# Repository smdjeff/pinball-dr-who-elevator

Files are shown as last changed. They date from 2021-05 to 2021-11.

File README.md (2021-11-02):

# dr-who

Replacement elevator mechanism for the Dr Who pinball machine. 

https://en.wikipedia.org/wiki/Doctor_Who_(pinball)

https://youtu.be/fHkql48IPpg

https://youtu.be/L-MsUkgBwkI

<table><tr>
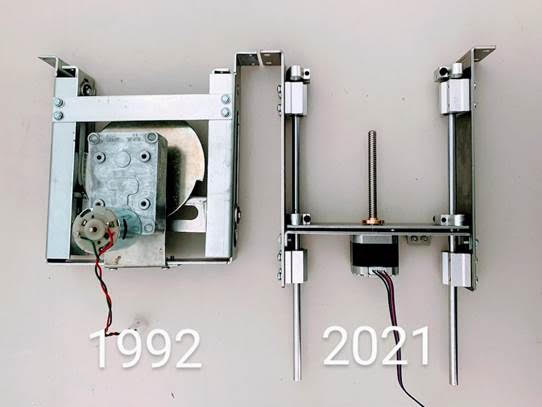
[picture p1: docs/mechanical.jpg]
<td rowspan="2"></td>
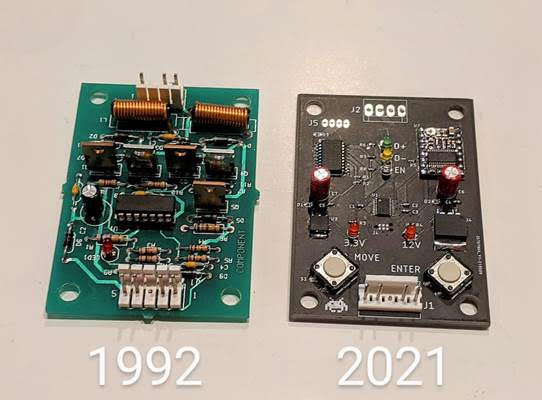
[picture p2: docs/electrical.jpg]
<td rowspan="2"></td>
</tr>
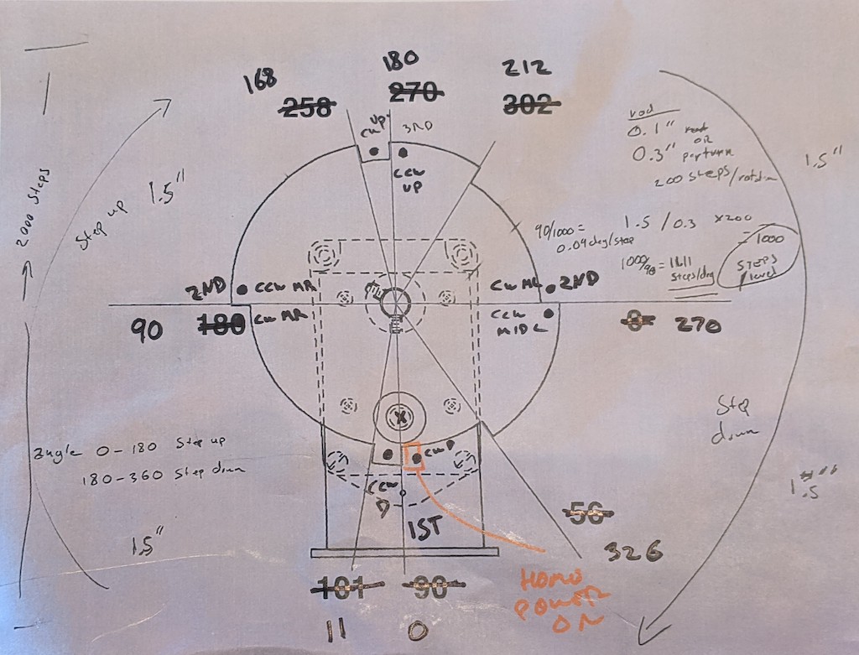
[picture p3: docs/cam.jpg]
<tr><td></td></tr>
</table>

## Firmware
* Drop in replacement to original system
* Uses simulated cam stimulus into factory system
* Passes factory diagnostics tests 

## Electronics
* Custom electronics
* Drop in replacement for bi-directional motor board A-15782
* Modern current limiting for saftey
* Modern acceleration and deceleration profiles for smooth start and stop

## Mechanical
* Custom brackets - laser cut and bent
* Standard desktop CNC stepper motor, rod, and nut.
* Replaces original parts
  * Cam A-15035
  * Motor 14-7970
  * Bracket A-15037
  * Support Bracket A-15036
  * Roller 02-4764

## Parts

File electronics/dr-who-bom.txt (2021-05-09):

Partlist exported from /Users/jmathews/Documents/EAGLE/projects/dr-who.sch at 5/8/21 1:46 PM

Part Value         Device                           Package                 Description                                                               MF    MPN           OC_FARNELL OC_NEWARK POPULARITY PROD_ID   VALUE
C1   4.7uF         4.7UF0603                        0603                    4.7µF ceramic capacitors                                                                                                      CAP-08280 4.7uF
C2   0.1uF         0.1UF-0603-25V-(+80/-20%)        0603                    0.1µF ceramic capacitors                                                                                                      CAP-00810 0.1uF
C3   0.1uF         0.1UF-0603-25V-(+80/-20%)        0603                    0.1µF ceramic capacitors                                                                                                      CAP-00810 0.1uF
C4   0.47uF        470PF-0603-50V-5%                0603                    470pF ceramic capacitors                                                                                                      CAP-07884 470pF
C5   0.47uF        470PF-0603-50V-5%                0603                    470pF ceramic capacitors                                                                                                      CAP-07884 470pF
C6   100uF         100UF-POLAR-RADIAL-2.5MM-25V-20% CPOL-RADIAL-2.5MM-6.5MM 100µF polarized capacitors                                                                                                    CAP-08439 100uF
C7   100uF         100UF-POLAR-RADIAL-2.5MM-25V-20% CPOL-RADIAL-2.5MM-6.5MM 100µF polarized capacitors                                                                                                    CAP-08439 100uF
D1                 DIODE-SOD323-R                   SOD323-R                DIODE                                                                                                              4                         
D2                 DIODE-SOD323-R                   SOD323-R                DIODE                                                                                                              4                         
D3                 DIODE-SOD323-R                   SOD323-R                DIODE                                                                                                              4                         
J1                 KK-156-5                         KK-156-5                KK 156 HEADER                                                             MOLEX               unknown    unknown   0                         
J2                 KK-156-4                         KK-156-4                KK 156 HEADER                                                             MOLEX               unknown    unknown   0                         
J4                 TC2030-MCP-NL                    TC2030-MCP-NL           TAG-CONNECT ICSP ConnectorManufacturer: Tag-Connect                                                                                          
J5                 PINHD-1X4                        1X04                    PIN HEADER                                                                                                         91                        
LED1 3.3V          LED3MM                           LED3MM                  LED                                                                                                                97                        
LED2 12V           LED3MM                           LED3MM                  LED                                                                                                                97                        
LED3 D+            LED3MM                           LED3MM                  LED                                                                                                                97                        
LED4 D-            LED3MM                           LED3MM                  LED                                                                                                                97                        
LED5 EN            LED3MM                           LED3MM                  LED                                                                                                                97                        
R1   10k           10KOHM-0603-1/10W-1%             0603                    10kΩ resistor                                                                                                                 RES-00824 10k  
R2   10k           10KOHM-0603-1/10W-1%             0603                    10kΩ resistor                                                                                                                 RES-00824 10k  
R3   650           10KOHM-0603-1/10W-1%             0603                    10kΩ resistor                                                                                                                 RES-00824 10k  
R4   5k            10KOHM-0603-1/10W-1%             0603                    10kΩ resistor                                                                                                                 RES-00824 10k  
R5   100k          10KOHM-0603-1/10W-1%             0603                    10kΩ resistor                                                                                                                 RES-00824 10k  
R6   470           10KOHM-0603-1/10W-1%             0603                    10kΩ resistor                                                                                                                 RES-00824 10k  
R7   470           10KOHM-0603-1/10W-1%             0603                    10kΩ resistor                                                                                                                 RES-00824 10k  
R8   470           10KOHM-0603-1/10W-1%             0603                    10kΩ resistor                                                                                                                 RES-00824 10k  
S1   MOVE          40/XX                            B3F/40XX                OMRON SWITCH                                                                                  unknown    unknown   0                         
S2   ENTER         40/XX                            B3F/40XX                OMRON SWITCH                                                                                  unknown    unknown   0                         
U1   STM32L011F3P6 STM32L011F3P6                    TSSOP20-I               IC                                                                                                                                           
U2   2977-DRV8825  2977-DRV8825                     DRV8825                 DRV8825 Stepper Motor Driver Carrier; High Current (Bulk; No Header Pins)                                                                    
U3   LM2936DT-3.3  LM2936DT-3.3                     TO252                   Ultra-Low Quiescent Current LDO Voltage Regulator                               BD433M5FP-CE2 1286863    26M0361   0                         
U4   LM2936D2PAK   LM2936D2PAK                      D2PAK                   Ultra-Low Quiescent Current LDO Voltage Regulator                                                                                            
U5   MAX333ACWP    MAX333ACWP                       SO20L                   ANALOG SWITCH                                                             MAXIM MAX333ACWP+   9725547    28K3302   0

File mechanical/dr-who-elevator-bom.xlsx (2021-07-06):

Table 1
Price sub | QTY | Part number
$8.23 | 1 | 500001 | Travel plate
$14.50 | 2 | 500002 | Side plate
$12.84 | 1 | 500003 | Motor plate
$0.00 | 0 | 500004-1 | Support shaft | Not used
$9.99 | 2 | 500004-2 | Support shaft
$11.98 | 4 | PN? | Bearing slide | 8mm
$9.99 | 2 | PN? | Rod | 8mm x 300mm
$25.99 | 1 |  | Stepper w/ rod | T8 100mm | What’s the spec on this? Comes with cable?
$0.00 | 1 | PN? | Rod nut
$0.58 | 1 | PN? | Micro switch
$3.00 | 1 |  | Screws | Specs?
$25.00 | 1 |  | PCB ASSY
$122.10

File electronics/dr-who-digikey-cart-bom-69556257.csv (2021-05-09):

# | QUANTITY | PART NUMBER | MANUFACTURER PART NUMBER | DESCRIPTION | CUSTOMER REFERENCE | BACKORDER | UNIT PRICE | EXTENDED PRICE
1 | 10 | 311-4047-1-ND | CC0603KRX5R9BB474 | CAP CER 0.47UF 50V X5R 0603 | C4,C5 | 0 | 0.35800 | 3.58
2 | 10 | 732-8825-1-ND | 860020473008 | CAP ALUM 100UF 20% 25V RADIAL | C6,C7 | 0 | 0.13000 | 1.30
3 | 15 | 1727-1228-1-ND | PMEG2010EA,135 | DIODE SCHOTTKY 20V 1A SOD323 | D1,D2,D3 | 0 | 0.28400 | 4.26
4 | 5 | A19903-ND | 640388-5 | CONN HEADER VERT 5POS 3.96MM | J1 | 0 | 0.37000 | 1.85
5 | 5 | A19902-ND | 640388-4 | CONN HEADER VERT 4POS 3.96MM | J2 | 0 | 0.32000 | 1.60
6 | 10 | 311-10KLECT-ND | AC0603JR-0710KL | RES SMD 10K OHM 5% 1/10W 0603 | R1,R2 | 0 | 0.02400 | 0.24
7 | 10 | SW411-ND | B3F-4000 | SWITCH TACTILE SPST-NO 0.05A 24V | S1,S2 | 0 | 0.44600 | 4.46
8 | 5 | BD433M5FP-CE2CT-ND | BD433M5FP-CE2 | IC REG LINEAR 3.3V 500MA TO252-3 | U3 | 0 | 1.07000 | 5.35
9 | 5 | LM2940CSX-12/NOPBCT-ND | LM2940CSX-12/NOPB | IC REG LIN 12V 1A DDPAK/TO263-3 | U4 | 0 | 1.93000 | 9.65
10 | 10 | 311-3567-1-ND | CC0603KPX7R9BB104 | CAP CER 0.1UF 50V X7R 0603 | C2,C3 | 0 | 0.06200 | 0.62
11 | 10 | 311-1455-1-ND | CC0603KRX5R6BB475 | CAP CER 4.7UF 10V X5R 0603 | C1 | 0 | 0.19500 | 1.95
12 | 10 | 311-10.0KHRCT-ND | RC0603FR-0710KL | RES SMD 10K OHM 1% 1/10W 0603 | R1,R2 | 0 | 0.02400 | 0.24
13 | 10 | 311-649HRCT-ND | RC0603FR-07649RL | RES SMD 649 OHM 1% 1/10W 0603 | R3 | 0 | 0.02400 | 0.24
14 | 10 | 311-2629-1-ND | RT0603DRE075K05L | RES SMD 5.05KOHM 0.5% 1/10W 0603 | R4 | 0 | 0.09200 | 0.92
15 | 10 | 311-100KHRCT-ND | RC0603FR-07100KL | RES SMD 100K OHM 1% 1/10W 0603 | R5 | 0 | 0.02400 | 0.24
16 | 10 | 478-7798-1-ND | SD0603S040S0R2 | DIODE SCHOTTKY 40V 200MA 0603 | D1,D2,D3 | 0 | 0.30200 | 3.02
17 | 10 | 311-470DCT-ND | RT0603DRD07470RL | RES SMD 470 OHM 0.5% 1/10W 0603 | R6,R7,R8 | 0 | 0.14400 | 1.44
18 | 10 | 732-5006-ND | 151031SS06000 | LED RED DIFFUSED 3MM ROUND T/H |  | 0 | 0.17000 | 1.70
19 | 10 | 732-5008-ND | 151031VS06000 | LED GREEN DIFFUSED 3MM ROUND T/H |  | 0 | 0.16000 | 1.60
20 | 10 | 732-5009-ND | 151031YS05900 | LED YELLOW DIFF 3MM ROUND T/H |  | 0 | 0.17000 | 1.70

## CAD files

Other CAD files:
mechanical/500002.dwg
mechanical/500003.dwg
mechanical/500001.dwg

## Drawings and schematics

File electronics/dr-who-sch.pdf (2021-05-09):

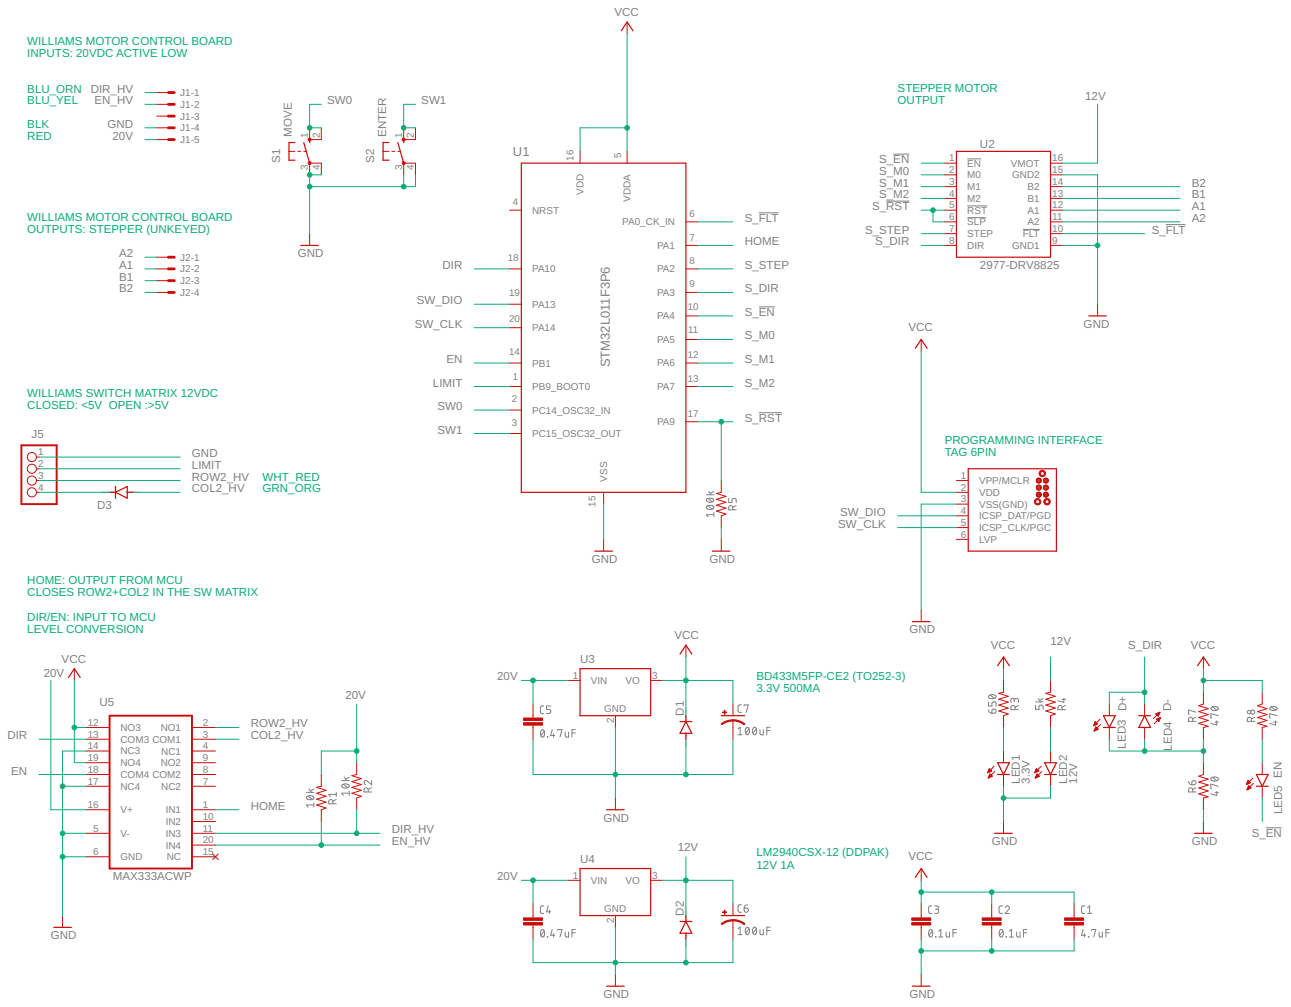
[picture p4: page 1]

WILLIAMS MOTOR CONTROL BOARD
INPUTS: 20VDC ACTIVE LOW

OUTPUTS: STEPPER (UNKEYED)

HOME: OUTPUT FROM MCU
CLOSES ROW2+COL2 IN THE SW MATRIX

DIR/EN: INPUT TO MCU
LEVEL CONVERSION

SpiceOrder 1 SpiceOrder 2

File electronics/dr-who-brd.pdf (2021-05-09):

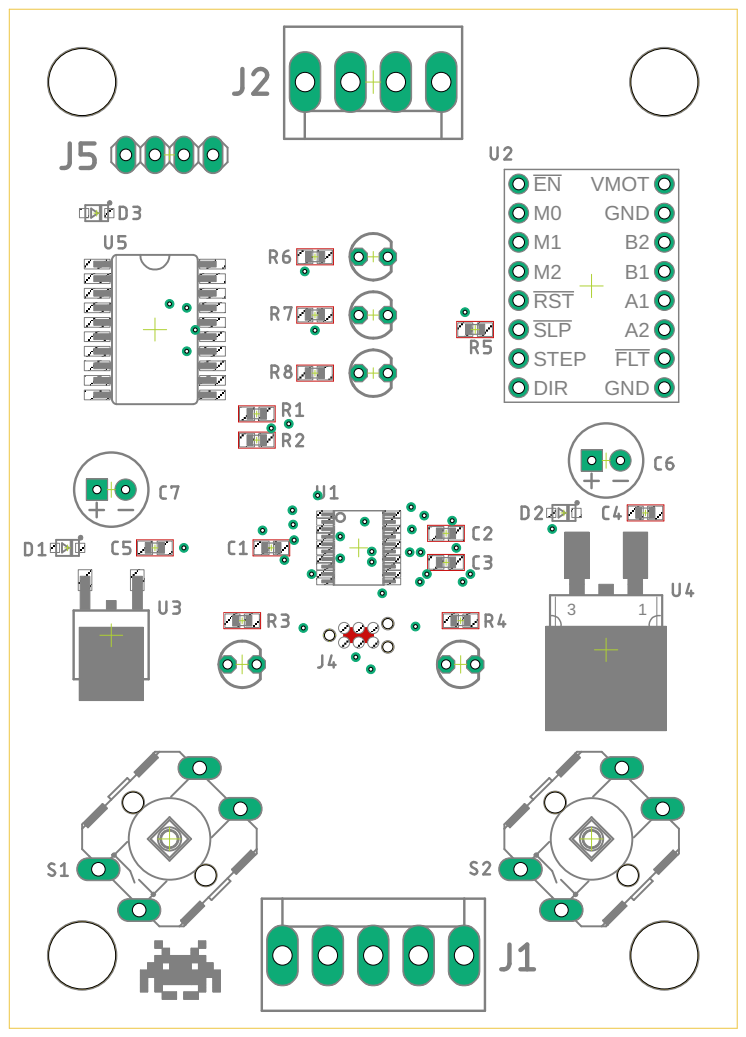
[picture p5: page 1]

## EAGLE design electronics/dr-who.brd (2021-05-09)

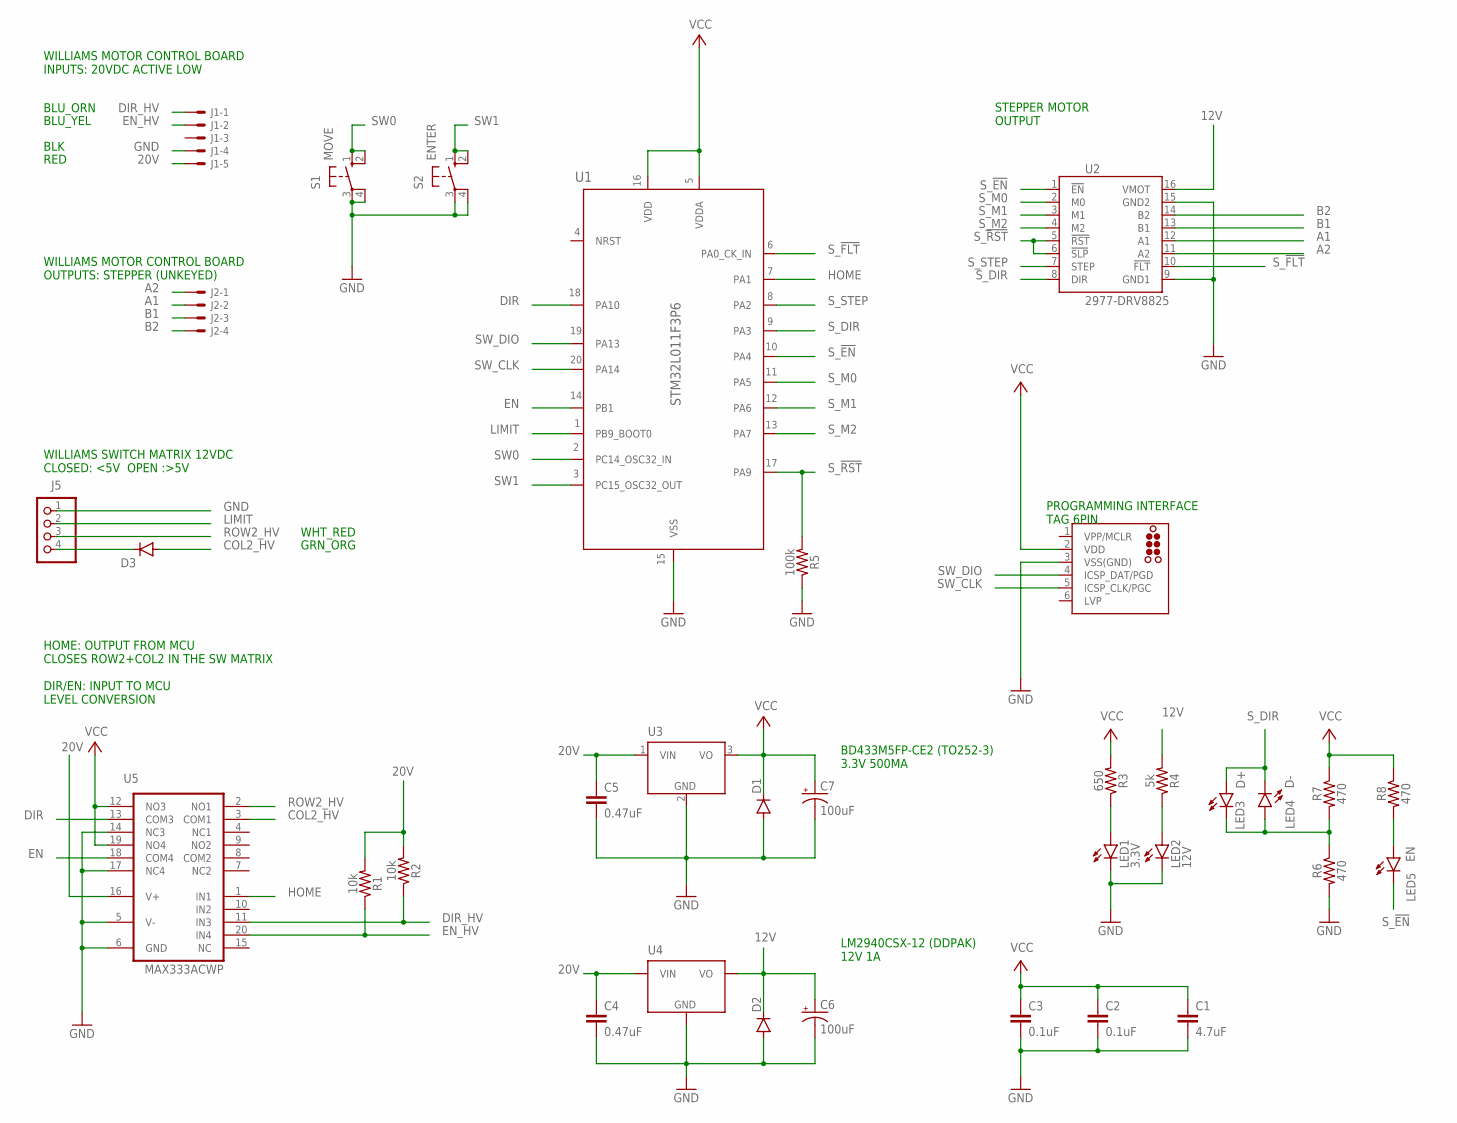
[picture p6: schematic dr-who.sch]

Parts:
C1: 4.7uF; 0603
C2, C3: 0.1uF; 0603
C4, C5: 0.47uF; 0603
C6, C7: 100uF; CPOL-RADIAL-2.5MM-6.5MM
D1, D2, D3: DIODE-SOD323-R; SOD323-R
J1: KK-156-5
J2: KK-156-4
J4: TC2030-MCP-NL
J5: PINHD-1X4; 1X04
LED1: 3.3V; LED3MM
LED2: 12V; LED3MM
LED3: D+; LED3MM
LED4: D-; LED3MM
LED5: EN; LED3MM
R1, R2: 10k; 0603
R3: 650; 0603
R4: 5k; 0603
R5: 100k; 0603
R6, R7, R8: 470; 0603
S1: MOVE; B3F/40XX
S2: ENTER; B3F/40XX
U1: STM32L011F3P6; TSSOP20-I
U2: 2977-DRV8825; DRV8825
U3: LM2936DT-3.3; TO252; MPN BD433M5FP-CE2
U4: LM2936D2PAK; D2PAK
U5: MAX333ACWP; SO20L

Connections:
12V: C6.1 (+), D2.C, R4.2, U2.16 (VMOT), U4.3 (VO)
20V: C4.1, C5.1, J1.5, R1.2, R2.2, U3.1 (VIN), U4.1 (VIN), U5.16 (V+)
A1: J2.2, U2.12 (A1)
A2: J2.1, U2.11 (A2)
B1: J2.3, U2.13 (B1)
B2: J2.4, U2.14 (B2)
COL2_HV: D3.A, U5.3 (COM1)
DIR: U1.18 (PA10), U5.13 (COM3)
DIR_HV: J1.1, R2.1, U5.11 (IN3)
EN: U1.14 (PB1), U5.18 (COM4)
EN_HV: J1.2, R1.1, U5.20 (IN4)
GND: C1.2, C2.2, C3.2, C4.2, C5.2, C6.2 (-), C7.2 (-), D1.A, D2.A, J1.4, J4.3 (VSS(GND)), J5.1, LED1.K (C), LED2.K (C), R5.1, R6.2, S1.3, S1.4 (P1), S2.3, S2.4 (P1), U1.15 (VSS), U2.9 (GND1), U2.15 (GND2), U3.2 (GND), U4.2 (GND), U5.5 (V-), U5.6 (GND), U5.14 (NC3), U5.17 (NC4)
HOME: U1.7 (PA1), U5.1 (IN1)
LIMIT: J5.2, U1.1 (PB9_BOOT0)
unnamed: D3.C, J5.4
unnamed: LED3.K (C), LED4.A, R6.1, R7.2
unnamed: LED5.A, R8.2
unnamed: LED1.A, R3.1
unnamed: LED2.A, R4.1
ROW2_HV: J5.3, U5.2 (NO1)
SW0: S1.1 (S), S1.2 (S1), U1.2 (PC14_OSC32_IN)
SW1: S2.1 (S), S2.2 (S1), U1.3 (PC15_OSC32_OUT)
SW_CLK: J4.5 (ICSP_CLK/PGC), U1.20 (PA14)
SW_DIO: J4.4 (ICSP_DAT/PGD), U1.19 (PA13)
S_!EN: LED5.K (C), U1.10 (PA4), U2.1 (!EN)
S_!FLT: U1.6 (PA0_CK_IN), U2.10 (!FLT)
S_!RST: R5.2, U1.17 (PA9), U2.5 (!RST), U2.6 (!SLP)
S_DIR: LED3.A, LED4.K (C), U1.9 (PA3), U2.8 (DIR)
S_M0: U1.11 (PA5), U2.2 (M0)
S_M1: U1.12 (PA6), U2.3 (M1)
S_M2: U1.13 (PA7), U2.4 (M2)
S_STEP: U1.8 (PA2), U2.7 (STEP)
VCC: C1.1, C2.1, C3.1, C7.1 (+), D1.C, J4.2 (VDD), R3.2, R7.1, R8.1, U1.5 (VDDA), U1.16 (VDD), U3.3 (VO), U5.12 (NO3), U5.19 (NO4)

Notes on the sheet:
BLU_ORN
BLU_YEL
RED
BLK
LM2940CSX-12 (DDPAK) 12V 1A
BD433M5FP-CE2 (TO252-3) 3.3V 500MA
WILLIAMS MOTOR CONTROL BOARD INPUTS: 20VDC ACTIVE LOW
PROGRAMMING INTERFACE TAG 6PIN
WHT_RED
GRN_ORG
WILLIAMS SWITCH MATRIX 12VDC CLOSED: <5V OPEN :>5V
STEPPER MOTOR OUTPUT
WILLIAMS MOTOR CONTROL BOARD OUTPUTS: STEPPER (UNKEYED)
HOME: OUTPUT FROM MCU CLOSES ROW2+COL2 IN THE SW MATRIX DIR/EN: INPUT TO MCU LEVEL CONVERSION

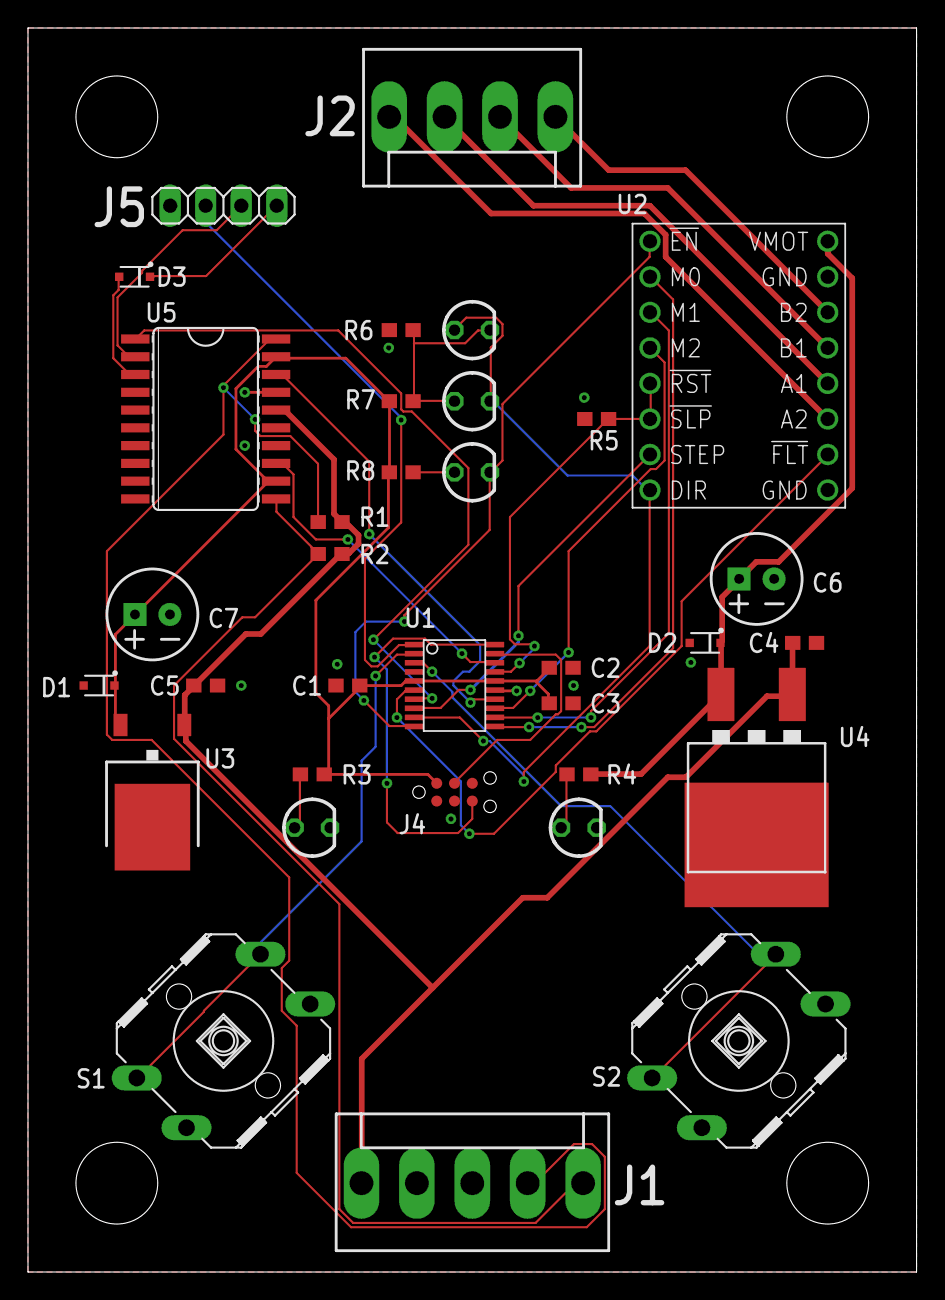
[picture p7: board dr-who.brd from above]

Board: 2 copper layers, 63.5 x 88.9 mm, 34 parts (0 on the bottom side), 33 nets.

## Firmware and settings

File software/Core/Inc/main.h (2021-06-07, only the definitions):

#define LIMIT_Pin LL_GPIO_PIN_9
#define LIMIT_GPIO_Port GPIOB
#define LIMIT_EXTI_IRQn EXTI4_15_IRQn
#define SW0_Pin LL_GPIO_PIN_14
#define SW0_GPIO_Port GPIOC
#define SW1_Pin LL_GPIO_PIN_15
#define SW1_GPIO_Port GPIOC
#define S_NFLT_Pin LL_GPIO_PIN_0
#define S_NFLT_GPIO_Port GPIOA
#define S_NFLT_EXTI_IRQn EXTI0_1_IRQn
#define HOME_Pin LL_GPIO_PIN_1
#define HOME_GPIO_Port GPIOA
#define S_STEP_Pin LL_GPIO_PIN_2
#define S_STEP_GPIO_Port GPIOA
#define S_DIR_Pin LL_GPIO_PIN_3
#define S_DIR_GPIO_Port GPIOA
#define S_NEN_Pin LL_GPIO_PIN_4
#define S_NEN_GPIO_Port GPIOA
#define S_M0_Pin LL_GPIO_PIN_5
#define S_M0_GPIO_Port GPIOA
#define S_M1_Pin LL_GPIO_PIN_6
#define S_M1_GPIO_Port GPIOA
#define S_M2_Pin LL_GPIO_PIN_7
#define S_M2_GPIO_Port GPIOA
#define EN_Pin LL_GPIO_PIN_10
#define EN_GPIO_Port GPIOA
#define S_NRST_Pin LL_GPIO_PIN_9
#define S_NRST_GPIO_Port GPIOA
#define DIR_Pin LL_GPIO_PIN_1
#define DIR_GPIO_Port GPIOB
#define NVIC_PRIORITYGROUP_0         ((uint32_t)0x00000007) /*!< 0 bit  for pre-emption priority,
#define NVIC_PRIORITYGROUP_1         ((uint32_t)0x00000006) /*!< 1 bit  for pre-emption priority,
#define NVIC_PRIORITYGROUP_2         ((uint32_t)0x00000005) /*!< 2 bits for pre-emption priority,
#define NVIC_PRIORITYGROUP_3         ((uint32_t)0x00000004) /*!< 3 bits for pre-emption priority,
#define NVIC_PRIORITYGROUP_4         ((uint32_t)0x00000003) /*!< 4 bits for pre-emption priority,

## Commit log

2021-05-09 stm32-mx for makefile (not stm32-ide)
2021-05-26 set reset pin correctly.
2021-05-26 attempt at stepper acceleration
2021-06-06 improved opto home output. inactivity timer.
2021-06-26 add nv storage for step adjustment. disable inactivity timer.
2021-07-06 add mechanical drawings
    [500001.dwg, 500002.dwg, 500003.dwg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]

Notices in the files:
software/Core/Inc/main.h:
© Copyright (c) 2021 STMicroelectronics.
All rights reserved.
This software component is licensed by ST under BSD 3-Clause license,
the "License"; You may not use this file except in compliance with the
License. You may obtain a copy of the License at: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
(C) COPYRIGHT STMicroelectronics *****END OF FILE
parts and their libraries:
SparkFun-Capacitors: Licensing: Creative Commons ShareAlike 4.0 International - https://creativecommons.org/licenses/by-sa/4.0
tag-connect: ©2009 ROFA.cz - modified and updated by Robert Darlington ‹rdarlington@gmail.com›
